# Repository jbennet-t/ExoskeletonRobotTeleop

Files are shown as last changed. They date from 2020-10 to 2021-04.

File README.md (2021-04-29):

# ExoskeletonRobotTeleop
Project centered around development of a wearable exoskeleton that translates user joint positions and movements in real time to a humanoid NAO robot.
Developed by Jordan Sinoway and Brian Dawson for 2021 Senior Capstone Project @ TCNJ

Exoskeleton embedded and Python code developed for Teensy 3.5 and NAO v4 robot, however could easily be reapplied to a new microcontroller and robot. Would suggest not using the NAO in the future due to reliability issues. 

This project is free to build and improve upon.

If you have any questions about the project, feel free to contact me.

## Exoskeleton Overview Model
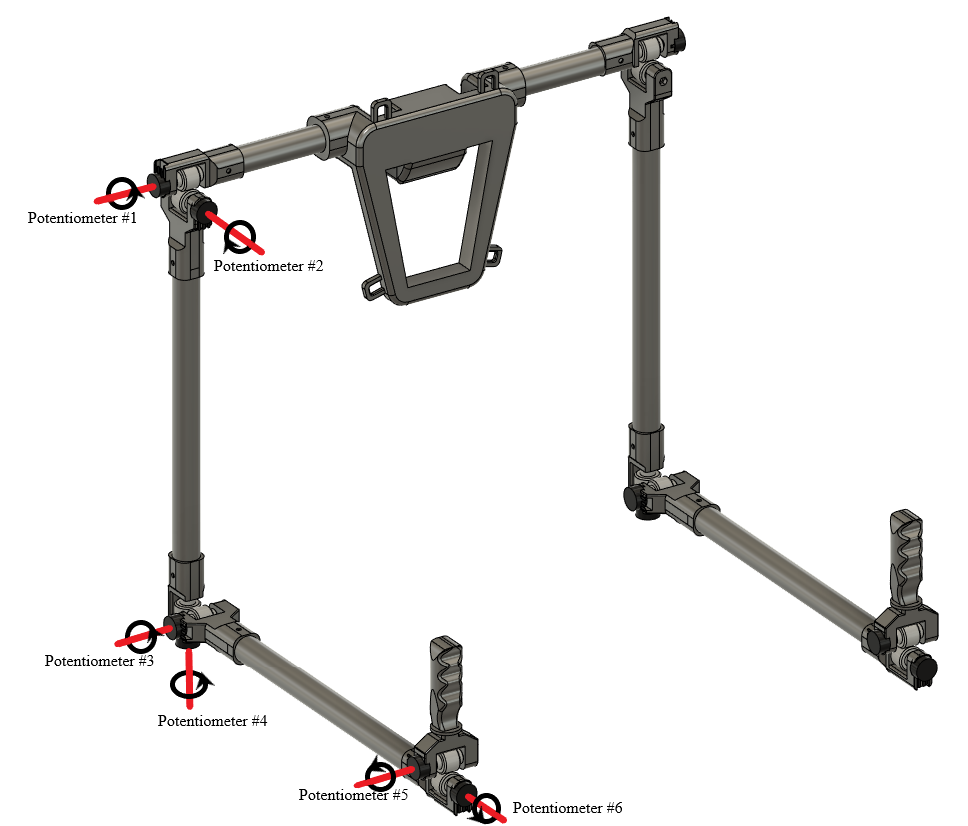
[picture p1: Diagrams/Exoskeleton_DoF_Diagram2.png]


## Abstract
The goal of this project is to create a novel exoskeleton apparatus that captures the movements of the wearer, and then translates these movements to a humanoid robot, granting approximately real-time teleoperation. The robot utilized for this project is Aldebaran Robotics’ NAO, a ⅓ scale humanoid robot. Teleoperation has many practical applications, including hazardous waste disposal, robotics surgery, and tasks in the military, space, sea, and medical sectors. Potentiometers are integrated into the mechanical design at key joints in the wrist, elbow, and shoulder of the exoskeleton. These sensors vary their voltage depending on the joint angle and these values are passed to the Teensy 3.5 microcontroller via a 13-bit ADC. The microcontroller then converts the data into usable angle measurements and passes them to a Python layer, via a serial data line, which in turn converts the angle measurements into commands the robot can interpret. The embedded code in the microcontroller is written in C++ and the Python intermediary layer utilizes Python 2.7 and the NAOqi SDK to control the robot. 

### What's Important
- Python_Intermediary_Layer.py - https://github.com/jbennet-t/ExoskeletonRobotTeleop/blob/master/Brian-Code/Python_Intermediary_Layer.py
- Everything in the Diagrams subdirectory
- Exoskeleton_main.ino https://github.com/jbennet-t/ExoskeletonRobotTeleop/blob/master/EmbeddedCode/exoskeleton_main/exoskeleton_main.ino
- Everything in the Exoskeleton_Models subdirectory (all stls are not up to date, should be regenerated)
- Exoskeleton_PCBv3: https://github.com/jbennet-t/ExoskeletonRobotTeleop/tree/master/PCB/Exoskeleton_PCBv3

### Materials List
Items required: (Approximate Cost ~$250)
- Teensy 3.5 Microcontroller (x1)
- Bourns PDF241-S425F Potentiometers (x12)
- STM LD1117 3.3V Fixed Voltage Regulator (x1)
- 3-Terminal Might-SPOX Molex Male Header (x12)
- 3-Terminal Might-SPOX Molex Female Header (x12)
- Film Capacitors (x3)
- Green Through-hole LED (x1)
- 2 Pole Switch (x1)
- M5 Bolts and Nuts (x20)
- 12ft USB 2.0 Cable (x1)
- ¾” PVC Pipe - 4ft Segment (x5)
- Backpack Straps (x2)
- 22 AWG Silicone Wire 40ft (x1)
- 3D Printed Components
- Printed Circuit Board
- Power Supply
- Laptop

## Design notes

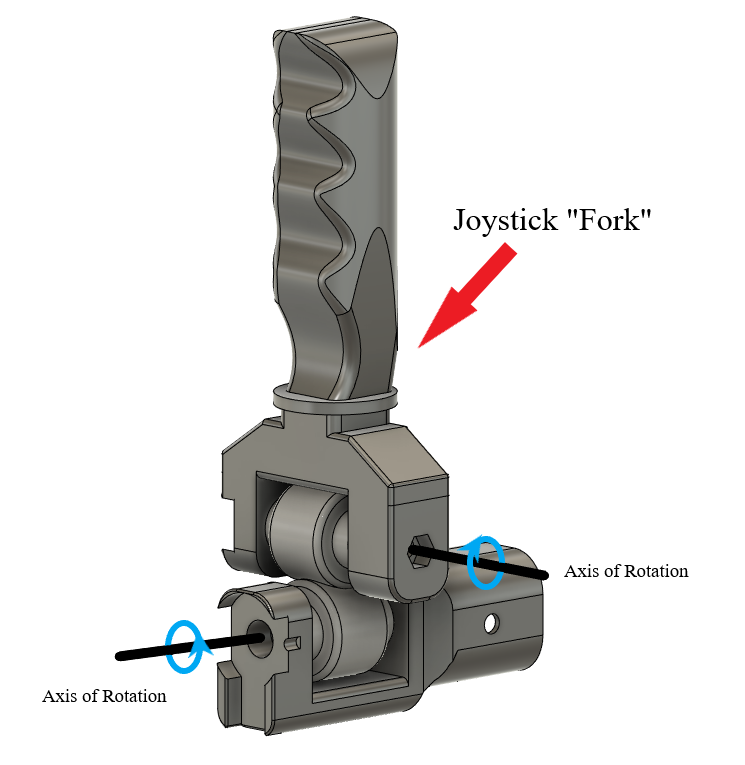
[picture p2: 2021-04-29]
Diagrams/Exoskeleton_wristjoint_diagram.png

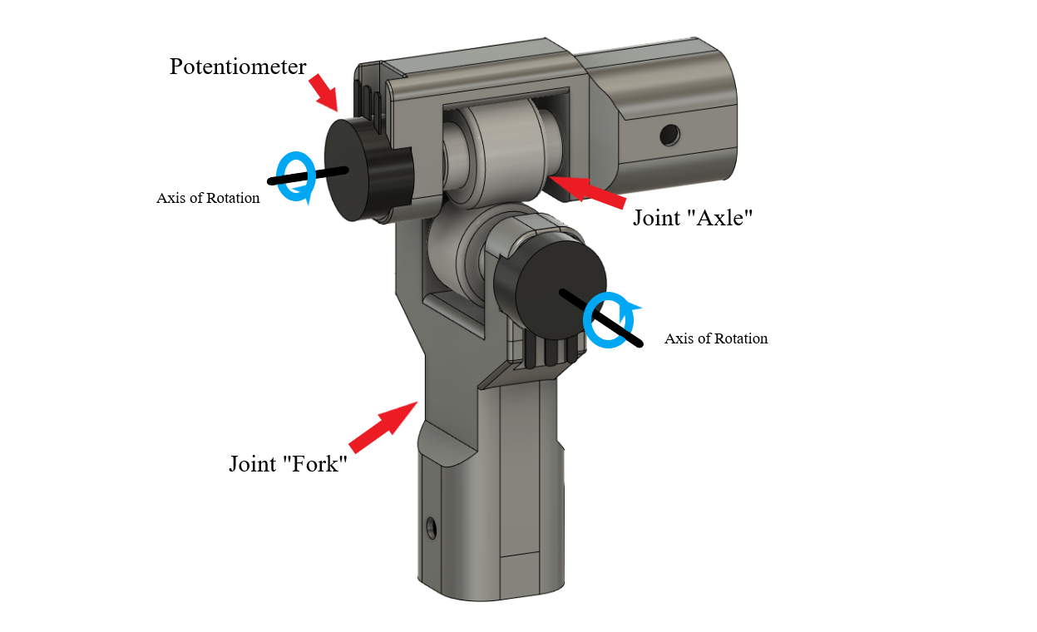
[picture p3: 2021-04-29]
Diagrams/Exoskeleton_shoulder_joint_diagram.png

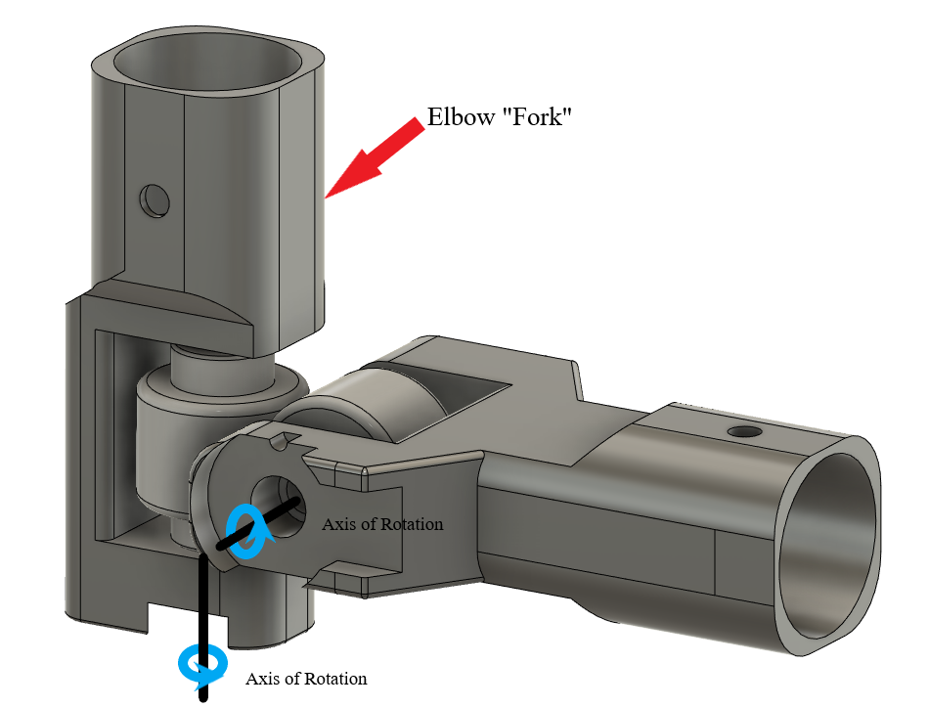
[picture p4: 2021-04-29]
Diagrams/Exoskeleton_elbowJoint_diagram.png

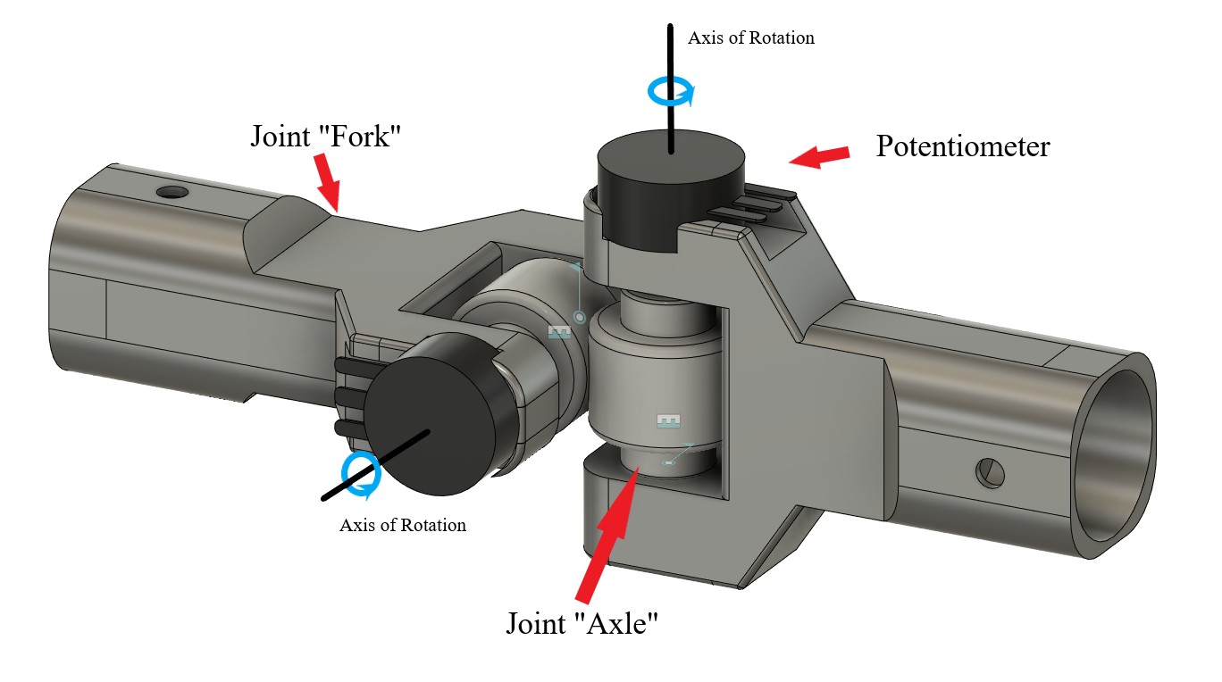
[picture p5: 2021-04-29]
Diagrams/Exoskeleton_joint_diagram.png

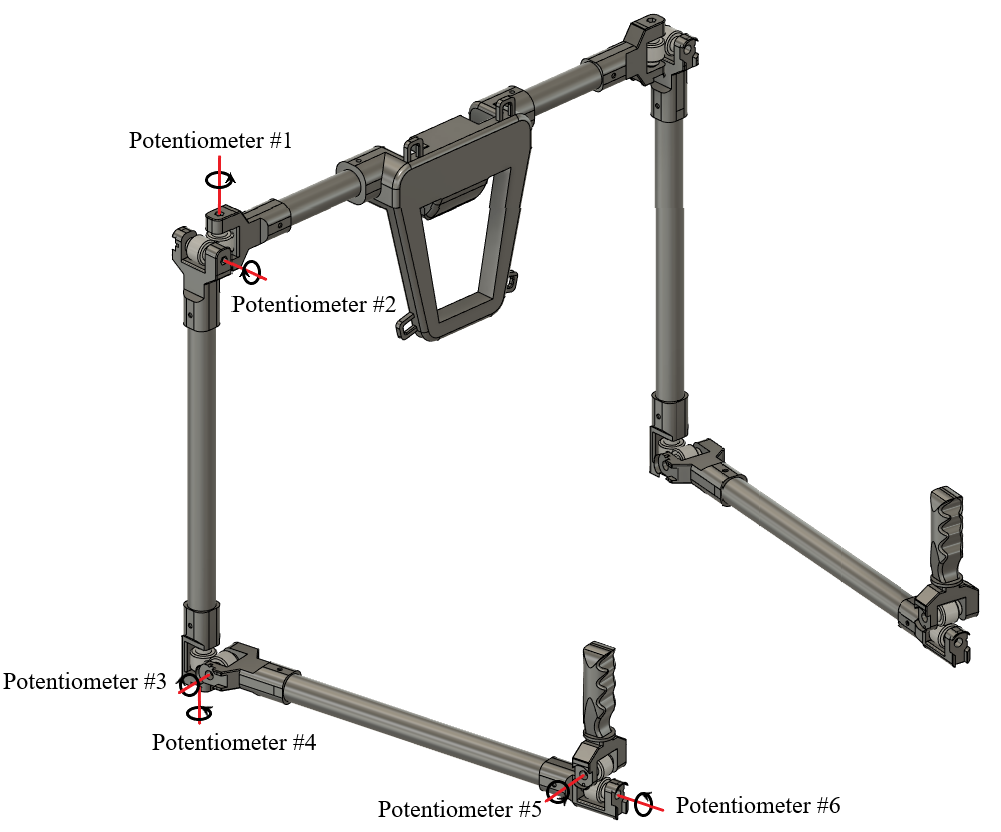
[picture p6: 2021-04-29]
Diagrams/Exoskeleton_DoF_Diagram.png

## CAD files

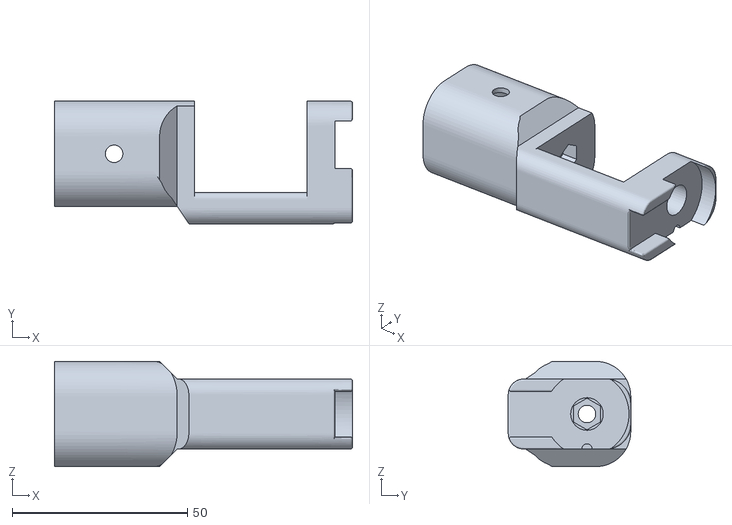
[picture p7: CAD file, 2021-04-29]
Exoskeleton_Models/STL_files/ElbowFork_4 v15.stl
85.0 x 35.0 x 30.0

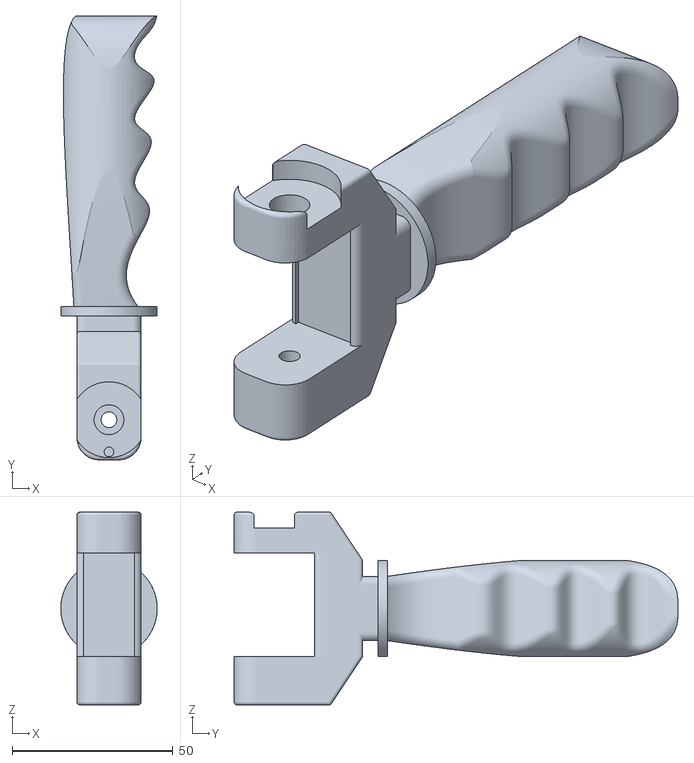
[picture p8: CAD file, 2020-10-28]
Exoskeleton_Models/STL_files/JoystickFork_1 v9.stl
30.0 x 138.0 x 60.0

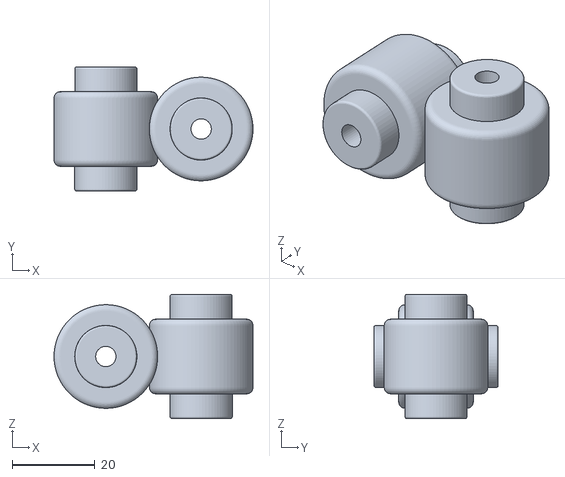
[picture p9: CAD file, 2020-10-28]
Exoskeleton_Models/STL_files/rAxle_1 v19.stl
48.0 x 30.0 x 30.0

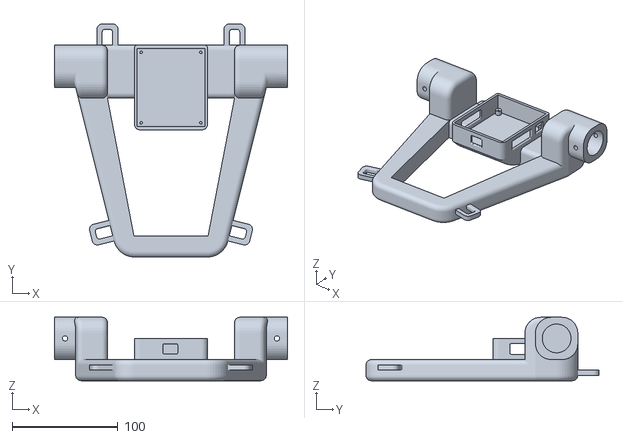
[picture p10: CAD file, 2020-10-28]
Exoskeleton_Models/STL_files/BackMount_1 v19.stl
220.0 x 220.0 x 60.0

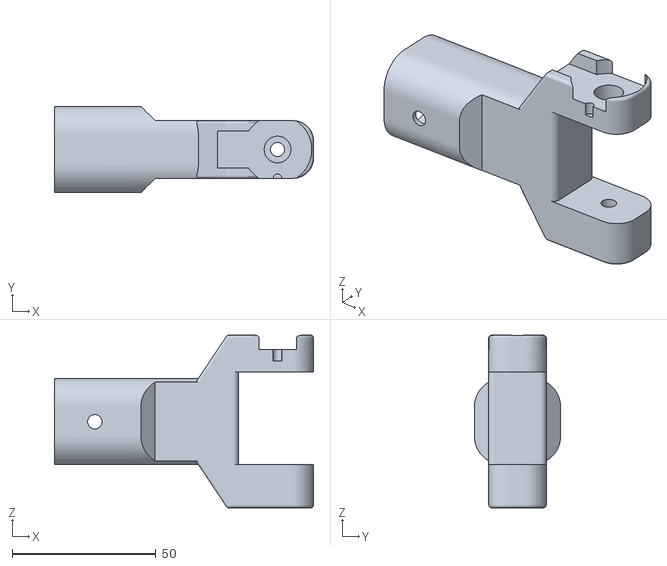
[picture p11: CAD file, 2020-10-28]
Exoskeleton_Models/STL_files/SholderFork_1 v20.stl
90.0 x 30.0 x 60.0

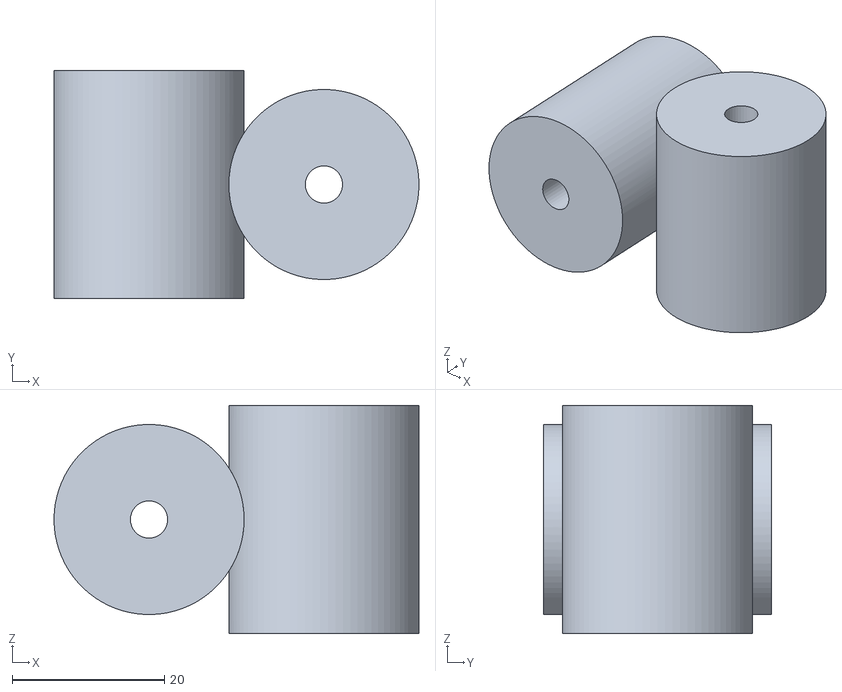
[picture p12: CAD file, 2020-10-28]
Exoskeleton_Models/STL_files/ShoulderAxle_1 v18.stl
48.0 x 30.0 x 30.0

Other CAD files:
Exoskeleton_Models/STL_files/ShoulderAxle_1 v17.stl
Exoskeleton_Models/BackMount_1 v20.f3d
Exoskeleton_Models/ElbowFork_4 v15.f3d
Exoskeleton_Models/JoystickFork_1 v10.f3d
Exoskeleton_Models/Overall_Assembly2 v12.f3z
Exoskeleton_Models/STL_files/Axle_1 v19.f3d
Exoskeleton_Models/SholderFork_1 v20.f3d
Exoskeleton_Models/ShoulderAxle_1 v20.f3d

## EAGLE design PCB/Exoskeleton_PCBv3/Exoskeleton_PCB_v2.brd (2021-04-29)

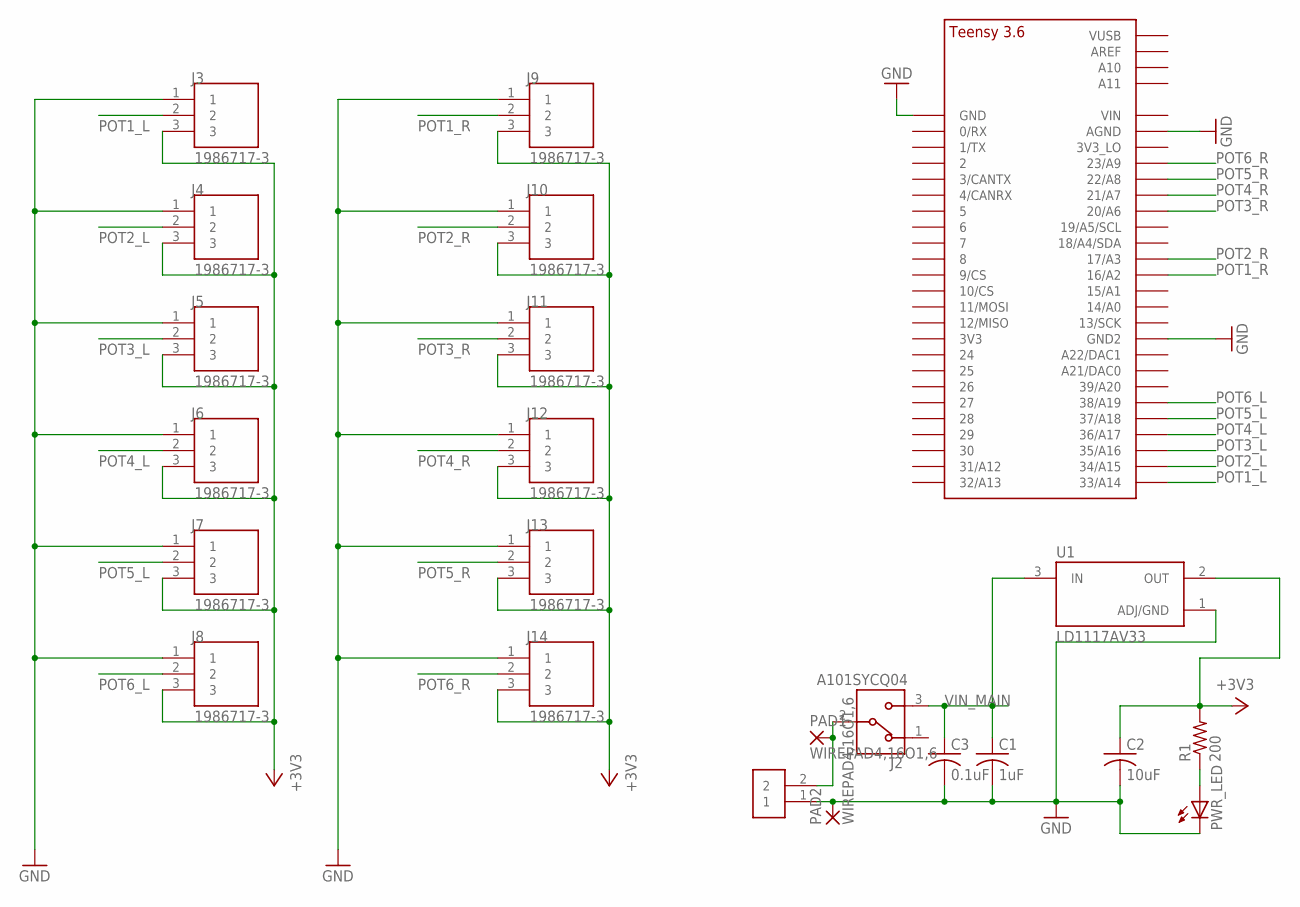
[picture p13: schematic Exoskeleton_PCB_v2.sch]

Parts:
C1: 1uF; C050-030X075
C2: 10uF; C050-030X075
C3: 0.1uF; C050-030X075
J1: 282837-2; TE_282837-2
J2: A101SYCQ04; TE_A101SYCQ04
J3, J4, J5, J6, J7, J8, J9, J10, J11, J12, J13, J14: 1986717-3; TE_1986717-3
PAD1, PAD2: WIREPAD4,16O1,6; 4,16O1,6
PWR_LED: LED5MM
R1: 200; 0207/9
U1: LD1117AV33; TO255P1020X450X1968-3
U$1: TEENSY_3.5/3.6_BASIC

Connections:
+3V3: C2.1, J3.3, J4.3, J5.3, J6.3, J7.3, J8.3, J9.3, J10.3, J11.3, J12.3, J13.3, J14.3, R1.2, U1.2 (OUT)
GND: C1.2, C2.2, C3.2, J1.1, J3.1, J4.1, J5.1, J6.1, J7.1, J8.1, J9.1, J10.1, J11.1, J12.1, J13.1, J14.1, PAD2.1, PWR_LED.K (C), U1.1 (ADJ/GND), U$1.AGND, U$1.GND, U$1.GND2
unnamed: PWR_LED.A, R1.1
unnamed: J1.2, J2.2, PAD1.1
POT1_L: J3.2, U$1.33/A14
POT1_R: J9.2, U$1.16/A2
POT2_L: J4.2, U$1.34/A15
POT2_R: J10.2, U$1.17/A3
POT3_L: J5.2, U$1.35/A16
POT3_R: J11.2, U$1.20/A6
POT4_L: J6.2, U$1.36/A17
POT4_R: J12.2, U$1.21/A7
POT5_L: J7.2, U$1.37/A18
POT5_R: J13.2, U$1.22/A8
POT6_L: J8.2, U$1.38/A19
POT6_R: J14.2, U$1.23/A9
VIN_MAIN: C1.1, C3.1, J2.3, U1.3 (IN)

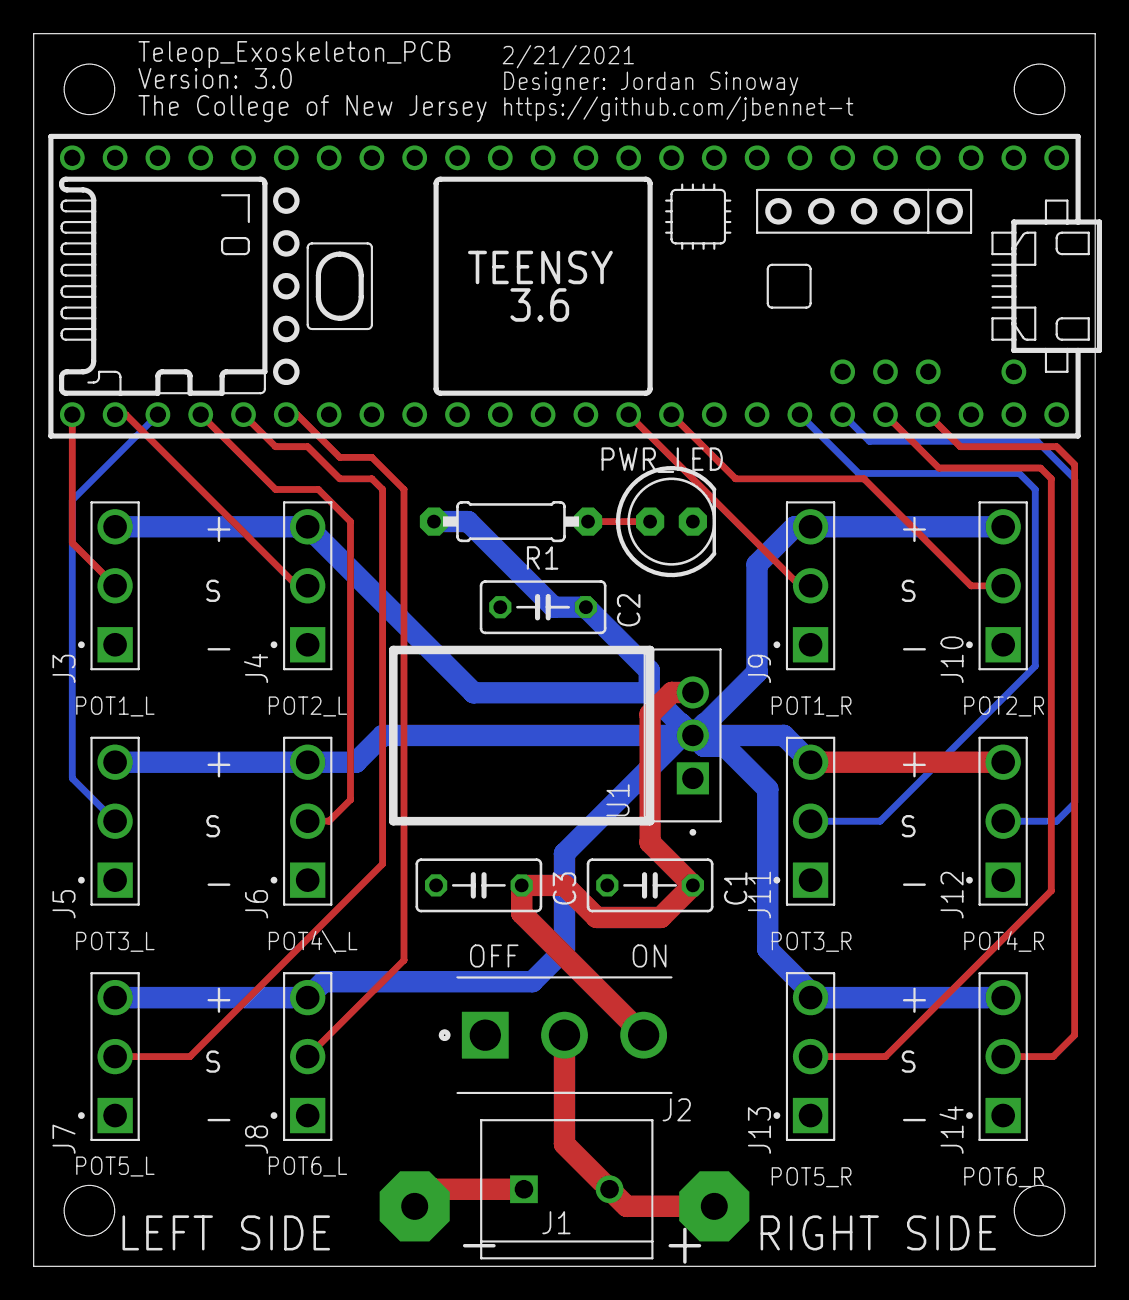
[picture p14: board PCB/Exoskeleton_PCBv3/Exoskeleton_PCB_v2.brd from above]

Board: 2 copper layers, 63.0 x 73.2 mm, 23 parts (0 on the bottom side), 17 nets.

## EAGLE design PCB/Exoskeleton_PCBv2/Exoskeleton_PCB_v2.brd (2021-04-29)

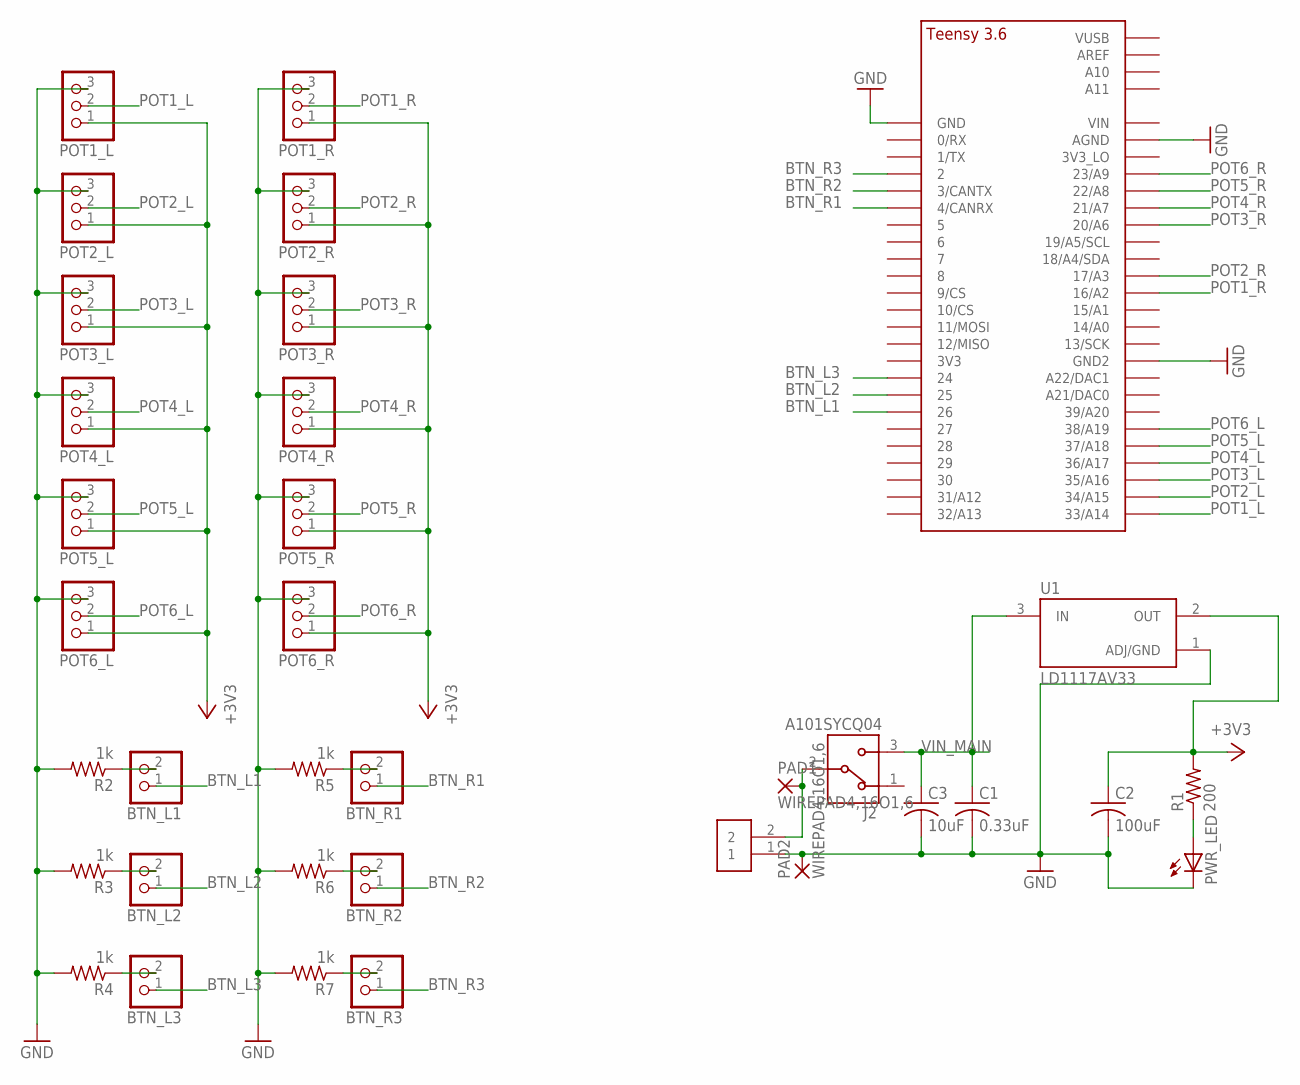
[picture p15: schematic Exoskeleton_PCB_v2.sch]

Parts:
BTN_L1, BTN_L2, BTN_L3: PINHD-1X2; 1X02
BTN_R1, BTN_R2, BTN_R3: PINHD-1X2; 1X02
C1: 0.33uF; C050-030X075
C2: 100uF; C050-030X075
C3: 10uF; C050-030X075
J1: 282837-2; TE_282837-2
J2: A101SYCQ04; TE_A101SYCQ04
PAD1, PAD2: WIREPAD4,16O1,6; 4,16O1,6
POT1_L, POT1_R, POT2_L, POT2_R, POT3_L, POT3_R, POT4_L, POT4_R, POT5_L, POT5_R, POT6_L, POT6_R: PINHD-1X3; 1X03
PWR_LED: LED5MM
R1: 200; 0207/9
R2, R3, R4, R5, R6, R7: 1k; 0207/9
U1: LD1117AV33; TO255P1020X450X1968-3
U$1: TEENSY_3.5/3.6_BASIC

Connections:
+3V3: C2.1, POT1_L.1, POT1_R.1, POT2_L.1, POT2_R.1, POT3_L.1, POT3_R.1, POT4_L.1, POT4_R.1, POT5_L.1, POT5_R.1, POT6_L.1, POT6_R.1, R1.2, U1.2 (OUT)
BTN_L1: BTN_L1.1, U$1.26
BTN_L2: BTN_L2.1, U$1.25
BTN_L3: BTN_L3.1, U$1.24
BTN_R1: BTN_R1.1, U$1.4/CANRX
BTN_R2: BTN_R2.1, U$1.3/CANTX
BTN_R3: BTN_R3.1, U$1.2
GND: C1.2, C2.2, C3.2, J1.1, PAD2.1, POT1_L.3, POT1_R.3, POT2_L.3, POT2_R.3, POT3_L.3, POT3_R.3, POT4_L.3, POT4_R.3, POT5_L.3, POT5_R.3, POT6_L.3, POT6_R.3, PWR_LED.K (C), R2.2, R3.2, R4.2, R5.2, R6.2, R7.2, U1.1 (ADJ/GND), U$1.AGND, U$1.GND, U$1.GND2
unnamed: PWR_LED.A, R1.1
unnamed: BTN_L1.2, R2.1
unnamed: BTN_L3.2, R4.1
unnamed: BTN_L2.2, R3.1
unnamed: BTN_R1.2, R5.1
unnamed: BTN_R2.2, R6.1
unnamed: BTN_R3.2, R7.1
unnamed: J1.2, J2.2, PAD1.1
POT1_L: POT1_L.2, U$1.33/A14
POT1_R: POT1_R.2, U$1.16/A2
POT2_L: POT2_L.2, U$1.34/A15
POT2_R: POT2_R.2, U$1.17/A3
POT3_L: POT3_L.2, U$1.35/A16
POT3_R: POT3_R.2, U$1.20/A6
POT4_L: POT4_L.2, U$1.36/A17
POT4_R: POT4_R.2, U$1.21/A7
POT5_L: POT5_L.2, U$1.37/A18
POT5_R: POT5_R.2, U$1.22/A8
POT6_L: POT6_L.2, U$1.38/A19
POT6_R: POT6_R.2, U$1.23/A9
VIN_MAIN: C1.1, C3.1, J2.3, U1.3 (IN)

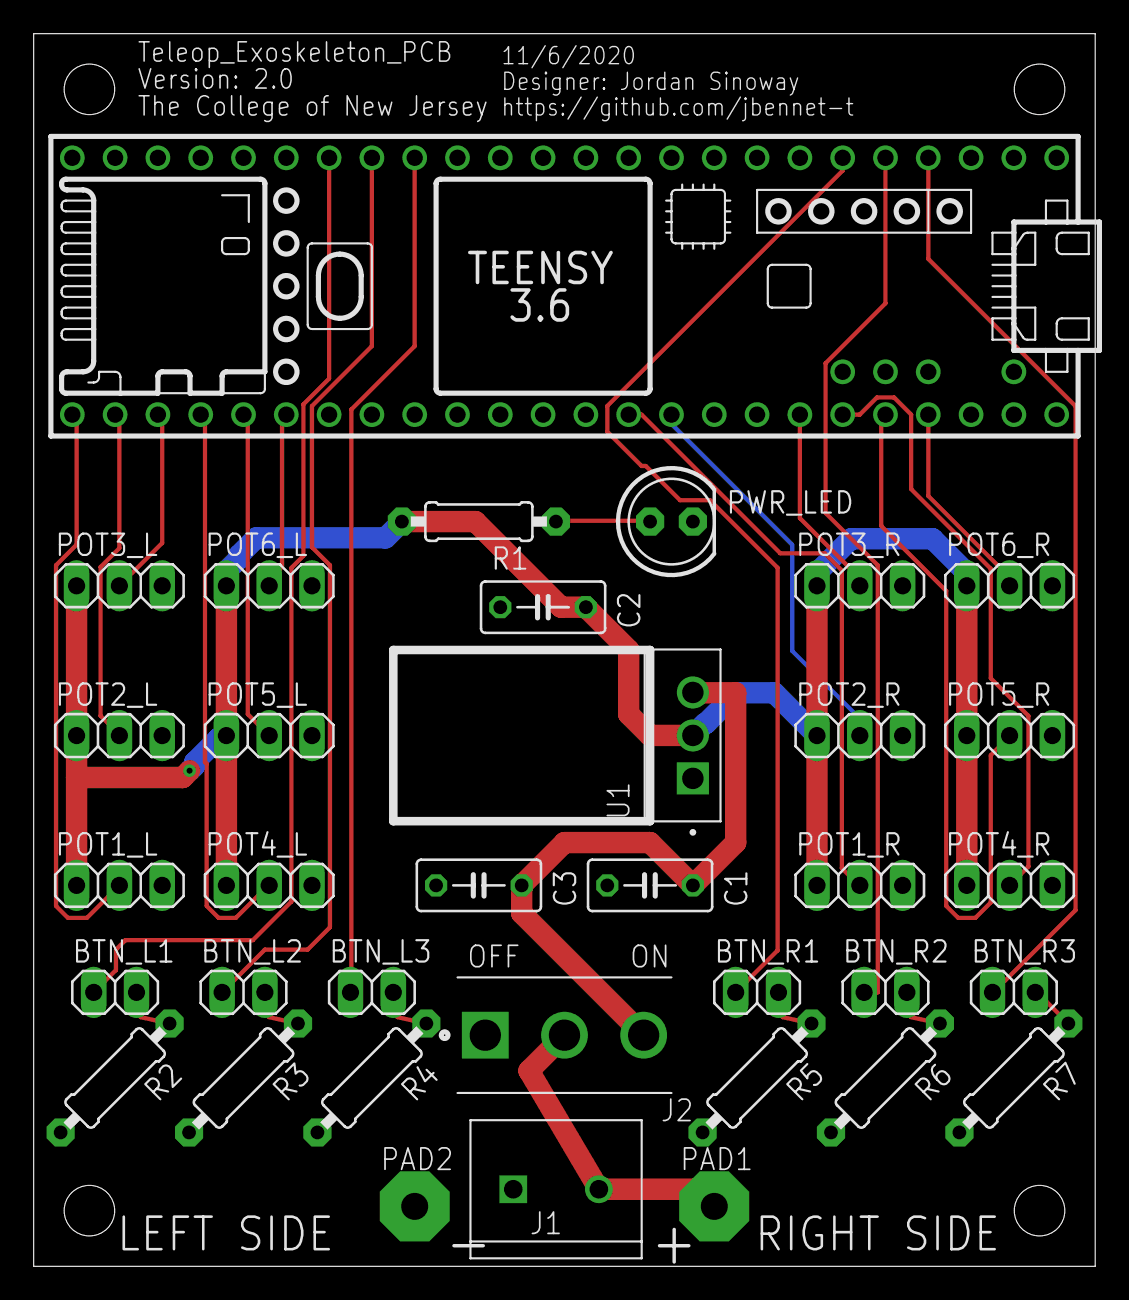
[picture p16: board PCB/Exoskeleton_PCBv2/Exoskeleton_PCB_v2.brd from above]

Board: 2 copper layers, 63.0 x 73.2 mm, 35 parts (0 on the bottom side), 29 nets.

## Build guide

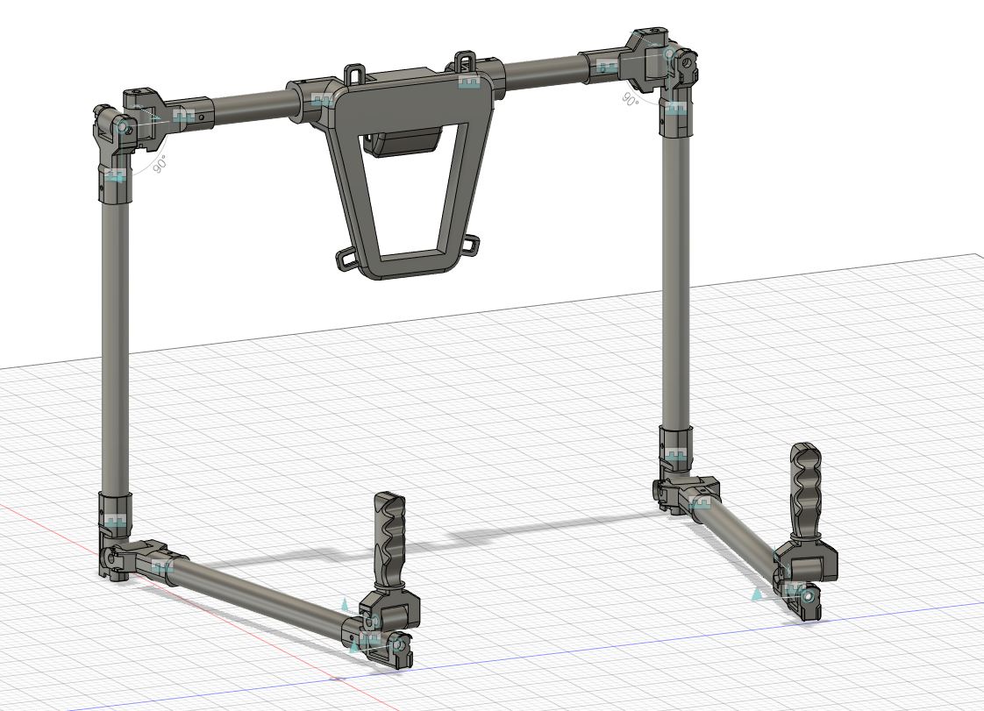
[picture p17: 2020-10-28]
Exoskeleton_Models/Overall_Assembly_picture.JPG

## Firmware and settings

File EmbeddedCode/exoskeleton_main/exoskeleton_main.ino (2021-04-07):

//program to transmit the readout data from one potentiometer 
//via serial to a python program

//arduino serial monitor must be closed to transmit serial data

#include <ResponsiveAnalogRead.h>

//Left side instantiation
const float potL1 = A14;  // analog pin used to connect the potentiometer
const float potL2 = A15;
const float potL3 = A16;
const float potL4 = A17;
const float potL5 = A18;
const float potL6 = A19;

//Right side instantiation
const int potR1 = A2;
const int potR2 = A3;
const int potR3 = A6;
const int potR4 = A7;
const int potR5 = A8;
const int potR6 = A9;

float aL1, aL2, aL3, aL4, aL5, aL6;
float aR1, aR2, aR3, aR4, aR5, aR6; //floats for later mapping

ResponsiveAnalogRead analogL1(potL1, true);
ResponsiveAnalogRead analogL2(potL2, true);
ResponsiveAnalogRead analogL3(potL3, true);
ResponsiveAnalogRead analogL4(potL4, true);
ResponsiveAnalogRead analogL5(potL5, true);
ResponsiveAnalogRead analogL6(potL6, true);

ResponsiveAnalogRead analogR1(potR1, true);
ResponsiveAnalogRead analogR2(potR2, true);
ResponsiveAnalogRead analogR3(potR3, true);
ResponsiveAnalogRead analogR4(potR4, true);
ResponsiveAnalogRead analogR5(potR5, true);
ResponsiveAnalogRead analogR6(potR6, true);

// make a ResponsiveAnalogRead object, pass in the pin, and either true or false depending on if you want sleep enabled
// enabling sleep will cause values to take less time to stop changing and potentially stop changing more abruptly,
// where as disabling sleep will cause values to ease into their correct position smoothly and more accurately


int val1;

void setup()                    
{
  Serial.begin(9600);     

  analogWriteResolution(13);//setting analog write/read resolution to 13 bits
  analogReadResolution(13);
  
  analogL1.setAnalogResolution(8192); //setting 13 bit resolution for responsiveanalogread objects
  analogL2.setAnalogResolution(8192);
  analogL3.setAnalogResolution(8192);
  analogL4.setAnalogResolution(8192);
  analogL5.setAnalogResolution(8192);
  analogL6.setAnalogResolution(8192);

  analogR1.setAnalogResolution(8192);
  analogR2.setAnalogResolution(8192);
  analogR3.setAnalogResolution(8192);
  analogR4.setAnalogResolution(8192);
  analogR5.setAnalogResolution(8192);
  analogR6.setAnalogResolution(8192);
}

void loop()                      
{
  analogL1.update(); //updates ResponsiveAnalogRead every loop
  analogL2.update();
  analogL3.update();
  analogL4.update();
  analogL5.update();
  analogL6.update();

  analogR1.update();
  analogR2.update();
  analogR3.update();
  analogR4.update();
  analogR5.update();
  analogR6.update();

  aL1 = analogL1.getValue(); //passing ResponsiveAnalogRead object vals to long variable
  aL2 = analogL2.getValue();
  aL3 = analogL3.getValue();
  aL4 = analogL4.getValue();
  aL5 = analogL5.getValue();
  aL6 = analogL6.getValue();

  aR1 = analogR1.getValue();
  aR2 = analogR2.getValue();
  aR3 = analogR3.getValue();
  aR4 = analogR4.getValue();
  aR5 = analogR5.getValue();
  aR6 = analogR6.getValue();

/*
  Serial.print(aL1); Serial.print(",");
  Serial.print(aL2); Serial.print(",");
  Serial.print(aL4); Serial.print(",");
  Serial.print(aL3); Serial.print(",");
  Serial.print(aL5); Serial.print(",");
  Serial.print("0"); Serial.print(","); //not yet used
  Serial.print(aR1); Serial.print(",");
  Serial.print(aR2); Serial.print(",");
  Serial.print(aR4); Serial.print(",");
  Serial.print(aR3); Serial.print(",");
  Serial.print(aR5); Serial.print(",");
  Serial.print("0"); //Serial.print(","); //not yet used
  */


  //mapping 13 bit ranges to radian ranges for Nao robots prior to pass over serial
  aL1 = map(aL1, 1100, 6570, -2.0857, 2.0857) + 1.20; //maps 13 bit range to radian range for shoulder pitch, pots go from 0-8191
  aL2 = map(aL2, 4690, 7190, -0.3142, 1.3265); //shoulder roll
  aL3 = map(aL3, 1602, 6995, -2.0857, 2.0857)* 1; //elbow yaw
  aL4 = map(aL4, 1430, 6570, -1.5446, -0.0349)* 1; //elbow roll
  aL5 = map(aL5, 1730, 7220, -1.8238, 1.8238); //wrist yaw
  aL6 = map(aL6, 0, 8191, -2.0857, 2.0857); //wrist roll - not used (for now)

  aR1 = map(aR1, 1240, 6609, -2.0857, 2.0857)*-1 + 1.20; //maps 13 bit range to radian range for shoulder pitch
  aR2 = map(aR2, 4407, 6721, -0.3142, 1.3265)* -1; //shoulder roll
  aR3 = map(aR3, 1770, 6780, -2.0857, 2.0857)* -1; //elbow yaw
  aR4 = map(aR4, 1947, 6553, -1.5446, -0.0349)* -1; //elbow roll
  aR5 = map(aR5, 1190, 6631, -1.8238, 1.8238)* -1; //wrist yaw
  aR6 = map(aR6, 0, 8191, -2.0857, 2.0857); //wrist roll - not used (for now)

/*
  Serial.print("0"); Serial.print(",");
  Serial.print("0"); Serial.print(",");
  Serial.print("-1"); Serial.print(",");
  Serial.print("0"); Serial.print(",");
  Serial.print("0"); Serial.print(",");
  Serial.print("0"); Serial.print(",");
  Serial.print(aL2); Serial.print(",");
  Serial.print(aL1); Serial.print(",");
  Serial.print(aL3); Serial.print(",");
  Serial.print(aL4); Serial.print(",");
  Serial.print(aL5); Serial.print(",");
  Serial.print("0"); //Serial.print(",");
 */


 //passing comma seperated vals to serial for transmission to Python program
  Serial.print(aL1); Serial.print(",");
  Serial.print(aL2); Serial.print(",");
  Serial.print(aL3); Serial.print(",");
  Serial.print(aL4); Serial.print(",");
  Serial.print(aL5); Serial.print(",");
  Serial.print("0"); Serial.print(","); //not yet used
  Serial.print(aR1); Serial.print(",");
  Serial.print(aR2); Serial.print(",");
  Serial.print(aR3); Serial.print(",");
  Serial.print(aR4); Serial.print(",");
  Serial.print(aR5); Serial.print(",");
  Serial.print("0"); //Serial.print(","); //not yet used
 
  
  /*
  Serial.print("\t");
  val1 = analog1.getValue();
  val1 = map(val1, 0, 8191, 0, 179);
  Serial.print(val1);

  if(analog1.hasChanged()) {
    Serial.print("\tchanged");
  }
  */
  Serial.println("");

  delay(50);                    
}

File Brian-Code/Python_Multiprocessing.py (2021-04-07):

import naoqi
import sys
import motion
import time
import argparse
import threading
import serial
import multiprocessing
from naoqi import ALProxy
from multiprocessing import Process

#IP and Port of the Nao
NAO_IP = "192.168.1.103"
PORT = 9559

#Ensuring the Nao Robot can be connected to properly
#Tries the varies different ALProxy methods used in code
try:
    motionProxy = ALProxy("ALMotion", NAO_IP, PORT)
except Exception, e:
    print "Could not create proxy to ALMotion"
    print "Error is ", e
else:
    motionProxy = ALProxy("ALMotion", NAO_IP, PORT)

try:
    autolifeProxy = ALProxy("ALAutonomousLife", NAO_IP, PORT)
except Exception, e:
    print "Could not create proxy to ALAutonomousLife"
    print "Error is ", e
else:
    autolifeProxy = ALProxy("ALAutonomousLife", NAO_IP, PORT)
    
try:
    postureProxy = ALProxy("ALRobotPosture", NAO_IP, PORT)
except Exception, e:
    print "Could not create proxy to ALRobotPosture"
    print "Error is", e
else:
    postureProxy = ALProxy("ALRobotPosture", NAO_IP, PORT)

#Disables the autonomous life mode
autolifeProxy.setState("disabled")

#Sets the sleeptime between commands to zero
#Sets speed of how fast robot moves from one position to another
sleeptime = 0.0
speed = 1.0


#Method used to control robot
#Takes in name of joint and the angle requested
def move_arm(names, angles):
    
    motionProxy.setAngles(names, angles, speed)
    time.sleep(sleeptime)


#Sets stiffness to zero and back to one in order to properly function
#Setting angles doesn't work without these commands
motionProxy.setStiffnesses("LArm", 0.0)
motionProxy.setStiffnesses("RArm", 0.0)
motionProxy.setStiffnesses("Body", 1.0)

#Go to sitting position to set robot to predetermined position
postureProxy.goToPosture("Stand" , 1.0)


#Setting serial port and baudrate for serial connection
print("Pre-serial test okay")
port = 'COM4'
baudrate = 9600

#Creating serial connection and flushing input
teensy3 = serial.Serial(port,baudrate)
teensy3.flushInput()

#Reference Information
# Shoulder Roll Range: -18 to 76 degrees (-.3142 to 1.3265 radians)
# Shoulder Pitch Range: -119.5 to 119.5 degrees (-2.0857 to 2.0857 radians)
# Elbow Yaw Range: -119.5 to 119.5 degrees (-2.0857 to 2.0857 radians)
# Elbow Roll Range: -88.5 to -2 degrees (-1.5446 to -0.0349 radians)
# Wrist Yaw Range: -104.5 to 104.5 degrees (-1.8238 to 1.8238 radians)




postureProxy.goToPosture("Stand" , 1.0)

#Always runs to ensure constant stream of information
while True:
    
    #Checking if the serial connection is open
    
    try:
        ser_bytes = teensy3.readline()
    except:
        print("Error in serial connection")
        break
    else:
    #Splitting the data into individual components
        ser_bytes = teensy3.readline()
        instruction_set = ser_bytes.split(",")
        #print (ser_bytes)
        #print (instruction_set)
    #Try statements to ensure data isn't missing
    #Replaces with zero if there is an issue with one of the potentiometers
    #Creates a new thread in order to interpt multiple movement commands at once
        try:
            angle1 = float(instruction_set[0])
        except:
            angle1 = 0
##        th1 = threading.Thread(target=move_arm, args = ("LShoulderPitch", angle1))
##        th1.start()
        th1 = Process(target = move_arm, args = ("LShoulderPitch", angle1))
        th1.start()
        #thread.start_new_thread(move_arm, ("LShoulderPitch", angle1))
        try:
            angle2 = float(instruction_set[1])
        except:
            angle2 = 0
        #thread.start_new_thread(move_arm, ("LShoulderRoll", angle2))
##        th2 = threading.Thread(target=move_arm, args = ("LShoulderRoll", angle2))
##        th2.start()
        th2 = Process(target = move_arm, args = ("LShoulderRoll", angle2))
        th2.start()
        try:
            angle3 = float(instruction_set[2])
        except:
            angle3 = -1
        #thread.start_new_thread(move_arm, ("LElbowRoll", angle3))
##        th3 = threading.Thread(target=move_arm, args = ("LElbowRoll", angle3))
##        th3.start()
        th3 = Process(target = move_arm, args = ("LElbowRoll", angle3))
        th3.start()
        try:
            angle4 = float(instruction_set[3])
        except:
            angle4 = 0
        #thread.start_new_thread(move_arm, ("LElbowYaw", angle4))
##        th4 = threading.Thread(target=move_arm, args = ("LElbowYaw", angle4))
##        th4.start()
        th4 = Process(target = move_arm, args = ("LElbowYaw", angle4))
        th4.start()
        try:
            angle5 = float(instruction_set[4])
        except:
            angle5 = 0
        #thread.start_new_thread(move_arm, ("LWristYaw", angle5))
##        th5 = threading.Thread(target=move_arm, args = ("LWristYaw", angle5))
##        th5.start()
        th5 = Process(target = move_arm, args = ("LWristYaw", angle5))
        th5.start()
        try:
          angle6 = float(instruction_set[6])
        except:
            angle6 = 0
        #thread.start_new_thread(move_arm, ("RShoulderPitch", angle6))
##        th6 = threading.Thread(target=move_arm, args = ("RShoulderPitch", angle6))
##        th6.start()
        th6 = Process(target = move_arm, args = ("RShoulderPitch", angle6))
        th6.start()
        try:
            angle7 = float(instruction_set[7])
        except:
            angle7 = 0
        #thread.start_new_thread(move_arm, ("RShoulderRoll", angle7))
##        th7 = threading.Thread(target=move_arm, args = ("RShoulderRoll", angle7))
##        th7.start()
        th7 = Process(target = move_arm, args = ("RShoulderRoll", angle7))
        th7.start()
        try:
            angle8 = float(instruction_set[8])
        except:
            angle8 = -1
        #thread.start_new_thread(move_arm, ("RElbowRoll", angle8))
##        th8 = threading.Thread(target=move_arm, args = ("RElbowRoll", angle8))
##        th8.start()
        th8 = Process(target = move_arm, args = ("RElbowRoll", angle8))
        th8.start()
        try:
            angle9 = float(instruction_set[9])
        except:
            angle9 = 0
        #thread.start_new_thread(move_arm, ("RElbowYaw", angle9))
##        th9 = threading.Thread(target=move_arm, args = ("RElbowYaw", angle9))
##        th9.start()
        th9 = Process(target = move_arm, args = ("RElbowYaw", angle9))
        th9.start()
        try:
            angle10 = float(instruction_set[10])
        except:
            angle10 = 0
        #thread.start_new_thread(move_arm, ("RWristYaw", angle10))
##        th10 = threading.Thread(target=move_arm, args = ("RWristYaw", angle10))
##        th10.start()
        th10 = Process(target = move_arm, args = ("RWristYaw", angle10))
        th10.start()

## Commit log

2020-10-25 added PCB directory, CAD directory, embedded code, python code
    [Axle_1 v19.f3d, BackMount_1 v19.f3d, BackMount_1 v19.stl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]
2020-11-06 probably fixed first try at getting serial working, added embbeded code
    [exoskeleton_main.ino, serialArduinoCom4.py]
2020-11-10 Fixed serial code and added error catching
    [testing.py]
2021-02-17 created new file for joint testing
2021-03-10 added right arm to embedded, some changes to python
2021-04-07 updating python and embedded code to current working version
2021-04-07 Made formatting of threading nicer
2021-04-29 April 2021 updates, finalized
    [Axle_1 v19.f3d, BackMount_1 v19.f3d, BackMount_1 v19.stl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]
